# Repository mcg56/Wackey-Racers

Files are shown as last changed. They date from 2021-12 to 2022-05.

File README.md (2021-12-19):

Wacky Racers
===============

This contains a directory structure for your assignment.

doc -- documentation

hw  -- hardware (add your schematic PDF here)

src -- source code

Assignment instructions
-----------------------

The [instructions](https://eng-git.canterbury.ac.nz/wacky-racers/wacky-racers/-/raw/master/doc/instructions/instructions.pdf) are in a PDF file stored in this repository (you'll also get a copy when you fork the project).

Assignment guide
----------------

The [guide](https://eng-git.canterbury.ac.nz/wacky-racers/wacky-racers/-/raw/master/doc/guide/guide.pdf) is a PDF file stored in this repository (you'll also get a copy when you fork the project).

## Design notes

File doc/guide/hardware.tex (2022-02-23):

\chapter{System design}
\label{hardware}

The system requirements are specified in the assignment instructions.

\section{Recommendations}\label{recommendations}

\begin{enumerate}
\item
  Independently fuse the buck converter and H-bridge. This allows a fuse
  to be removed to isolate part of the circuit when finding a fault,
  such as a short across the power rails.

\item
  Have a zener diode to protect against overvoltage when your group
  member inadvertently cranks up the voltage from the bench power
  supply.

\item
  Have current limiting resistors for all off-board signals.

\item
  Have plenty of testpoints, especially for power supplies and
  signals.  You will never have enough!

\item
  Have at least one grunty ground testpoint for attaching a scope ground
  clip.

\item
  Have a dedicated PIO pin to drive a testpoint that you can use to
  trigger an oscilloscope for debugging.

\item
  Have the SAM4S erase pin connected to a test point close to a 3.3\,V
  testpoint. This is useful to completely erase the SAM4S flash memory
  when nothing works.

\item
  Have a MOSFET or servo interface for controlling something dastardly!

\end{enumerate}

\section{Standard chassis}

You can build your own racer or use the standard chassis.  The
standard chassis comes with:
%
\begin{itemize}
\item A pair of 6\,V DC motors.

\item A bumper with microswitch.

\item An on/off switch and fuse for the battery.

\item Battery and holder.
\end{itemize}
%
It is available from Diego in the Electronics Lab.  If you wish to
make your own chassis, Diego can supply the bumper, battery, and
motors.

\begin{figure}[!h]
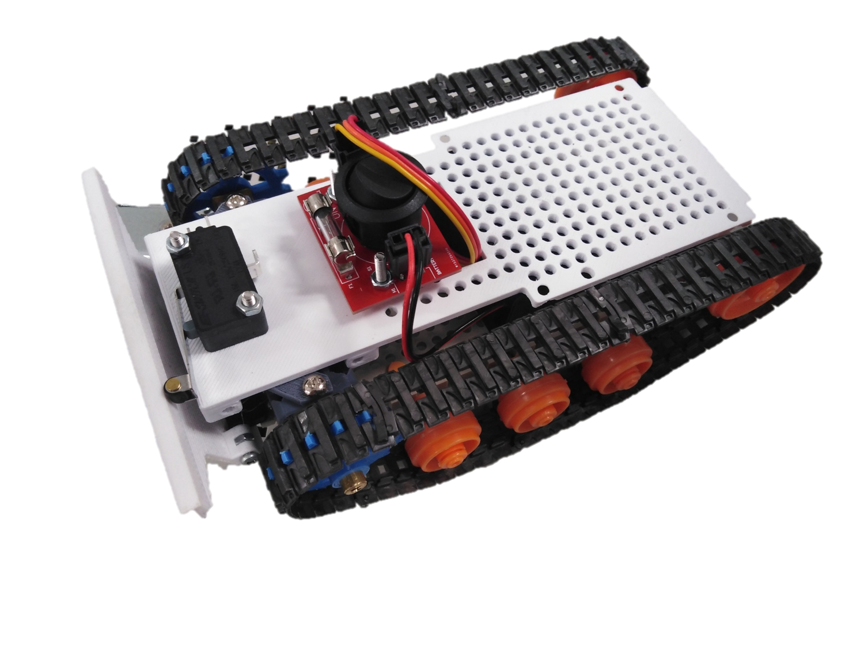
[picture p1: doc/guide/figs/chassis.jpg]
  \centering 
  \caption{Photo of the standard chassis.}
  \label{fig:chassis}
\end{figure}

\section{SAM4S MCU}\label{sam4s-mcu}

The SAM4S MCU is overkill for this assignment but is typical of ARM
processors used for bare-metal applications.  The particular chip we
are using is the SAM4S8B.  This was made by Atmel and is now owned by
Microchip.  The datasheet is available
at \url{https://www.microchip.com/en-us/product/ATSAM4S8B}.

The SAM4S8B has a 32-bit ARM Cortex M4 RISC CPU that can run at
120\,MHz and has 512\,KB of flash memory and 128\,KB of SRAM.

\subsection{Power pins}\label{power-pins}

The SAM4S has four grounds. They \textbf{must} all be connected. There
are also seven power pins. These \textbf{must} all be connected since
they power different parts of the chip. Note, some pins require 3.3\,V
while others require 1.2\,V. The 1.2\,V is generated by an internal
voltage regulator.

\subsection{Peripheral pins}\label{peripheral-pins}

\textbf{Many of the peripheral pins are dedicated and cannot be
  reassigned in software}, e.g., SPI, TWI, and USB pins. Note, there
are restrictions on the PWM pins.  See Table~11-2 in the SAM4S
datasheet for the pin assignments.  Also see \hyperref[PIO pins] {PIO
  pins} for electrical characteristics.

By default the \pin{PB4} and \pin{PB5} pins are configured for the
JTAG debugger.  These can be used for general PIO after setting an
internal bit.  See \protect\hyperref[disabling-jtag-pins]{disabling
JTAG pins}.

The logic levels are set by the voltage on the VDDIO pin (usually
3.3\,V).  \pin{PA12}--\pin{PA14} and \pin{PA26}--\pin{PA31} can
sink/source 4\,mA.  The USB pins (\pin{PB10}--\pin{PB11}) can
sink/source 30\,mA.  The rest can only sink/source 2\,mA of current.

The pullup and pulldown resistors are typically 100\,k$\Omega$.  On
reset, pullup resistors are enabled.

\subsection{USART/UART}\label{usartuart}

The SAM4S has two USARTs and two UARTs. The USARTs can emulate a
UART, have hardware flow control, and have a better driver so they are
recommended if you need a UART interface.

\subsection{PWM}\label{pwm}

The SAM4S can generate four independent PWM signals. There are
restrictions on which SAM4S pins they come out on. Note, the PWMLx and
PWMHx signals are complementary (i.e., one is low while the other is
high).

\subsection{TWI}\label{twi}

The SAM4S has two TWI peripherals (that can act as a master and
a slave) with dedicated TWD and TWCK pins. External pull-up resistors
are required.  TWI1 shares pins with JTAG; you will need to disable
JTAG in software.

\subsection{SPI}\label{spi}

The SAM4S has a single SPI peripheral with dedicated SCK, MISO, and
MOSI pins. Any PIO pin can be used for the chip select\footnote{For
  high speed operation (not needed for this assignment), you should
  use one of the dedicated chip select pins.}.

\subsection{ADC}\label{adc}

The SAM4S has a single ADC with a multiplexer to select one of a
number of analogue inputs.  It can sample at 1\,MHz.

\subsection{USB}\label{usb}

The SAM4S has a single USB peripheral connected to the DDP and DDM
pins. 27 ohm series termination resistors are required, placed close to
the SAM4S.

\section{Other chips}\label{other-chips}

\subsection{DRV8833 dual H-bridge}\label{drv8833-dual-h-bridge}

The DRV8833's datasheet is available at
\url{https://www.ti.com/product/DRV8833}.

The H-bridge has four modes: forward, reverse, slow decay (brake), and
fast decay (coast).  With slow decay mode, the motor is shorted so
that it stops faster.  With fast decay mode, the motor is
open-circuited and so it takes longer to stop.  However, there is
little difference in practice, due to friction in the gearbox.

If you want control over fast decay and slow decay in both forward and
reverse you will need \textbf{four} independent PWM signals. The SAM4S
can provide four independent PWM signals but be \textbf{careful} since
PWMxH and PWMxL are complementary signals driven from the same PWM
source.

If you are clever, you can drive the H-bridge with only two PWM
channels.  If you are not so clever, you will have fast decay in one
direction and slow decay in the other.

The capacitor connected to the bootstrap pin must be rated for
16\,V. The datasheet recommends an X7R dielectric.

\subsection{NRF24L01+ radio}

\begin{figure}[!h]
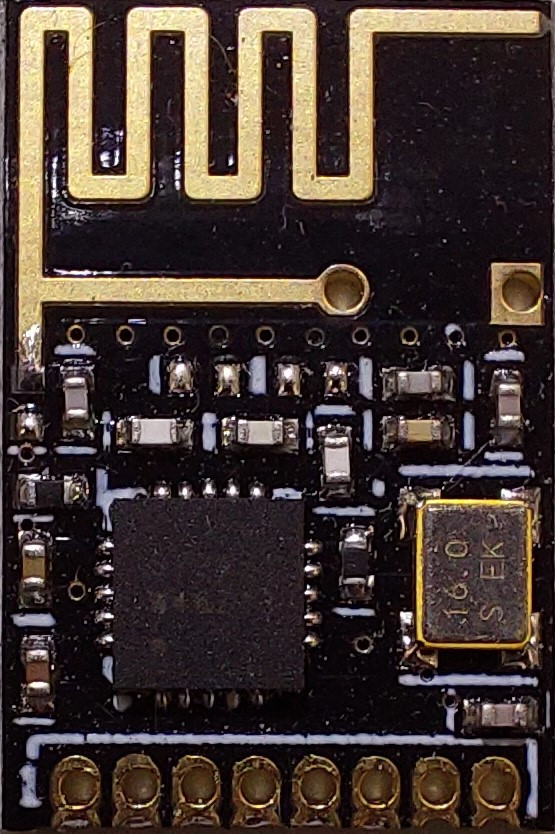
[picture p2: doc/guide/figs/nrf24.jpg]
  \centering 
  \caption{Photo of NRF24 radio.}
  \label{fig:nrf24}
\end{figure}

The nRF24 module we provide is actually a tiny PCB with all of the high
frequency analogue components populated for you. This module breaks out
the SPI communication pins, the power supply pins, and two signal pins
that you will need to connect to your microcontroller. The CE and IRQ
pins can both go to general PIO pins while the SPI pins (MOSI, MISO,
SCLK, CSN) need to be connected to the SAM4S SPI peripheral. The
nRF24L01 datasheet and other documentation for the breakout board is
available at \url{https://www.sparkfun.com/products/691}.

As this radio is ultimately an analogue circuit and any noise on the
power supply can affect the signal quality, we recommend using a
separate 3V3 regulator and using a low pass filter to provide the best
power.  Instead of a resistor, a ferrite bead is better.

\begin{figure}[h]
  \centering
  \begin{circuitikz}
    \draw (-1, 0) node[left] {\SI{3.3}{\volt}} to[R=\SI{1}{\ohm}, o-] (2, 0)
    to[C=\SI{10}{\micro\farad}, *-*] (2, -2);

    \draw (-1, -2) node[left] {GND} to[short, o-] (2, -2);
    \draw (2, 0) to[short] (4, 0);
    \draw (2, -2) to[short] (4, -2);
    \draw (6, 0.5) -- (4, 0.5) -- (4, -2.5) -- (6, -2.5);
    \node[right=0.2] at (4, 0) {VDD};
    \node[right=0.2] at (4, -2) {GND};
    \node at (6, -1) {nRF24};
  \end{circuitikz}
  \caption{Power supply filtering; a ferrite bead is better than a resistor.}
  \label{fig:radio-filtering}
\end{figure}

You cannot have a PCB plane near the antenna of the radio otherwise
the \textbf{range will be severely limited}.

The radio operates around 2.4 GHz and has 128 programmable channels,
each of 1 MHz.  Note, some of these channels use the same spectrum as
Bluetooth and WiFi.  A 5 byte address is appended to the start of each
transmission and the receiver will only respond when the address
matches.

The radio interfaces to the SAM4S using the SPI bus. The IRQ
pin is driven low to indicate a packet has been received.

\subsection{MPU9250 IMU}\label{mpu9250-imu}

This contains a three axis accelerometer, a three axis gyroscope, and a
three axis magnetometer. It appears that the magnetometer has been
bolted on to the accelerometers/gyroscopes and requires more hoop
jumping in software to make it work. Documentation is available at
\url{https://invensense.tdk.com/products/motion-tracking/9-axis/mpu-9250/}.

It has two different I2C addresses (0x68 and Ox69) depending on the
state of the AD0 pin.

\subsection{Buck converter}\label{buck-converter}

The buck converter is a switch-mode regulator that converts the
battery voltages to 5\,V DC.

\subsection{Voltage regulators}\label{voltage-regulators}

There are many flavours of \wikiref{voltage_regulators}{voltage regulator}.
Some are better for digital applications, some are better for analogue
applications, some are better for low power applications, etc.

If you are using a voltage regulator with an enable pin, do not forget
to allow for the time for the output voltage to ramp up. This can be
tens of milliseconds depending on the capacitive load and current draw.

Note, some regulators have pins that you must not connect. Some have
multiple pins for the same purpose; these must all be connected.

\section{External components}

\subsection{Battery}

The Wacky Racer batteries are Turnigy 5-cell 6\,V, 2300\,mAh, NiMH
with a three pin JST connector.  To preserve the battery life it is
imperative to not draw current when the battery voltage is below 5\,V.
Note, when fully charged, the battery voltage may be 7.5\,V.

The battery uses a standard RC servo connector: 3 pin 0.1'' (pin 1
GND, pin 2 5V, pin 3 NC). We suggest connecting both the first and
third pins to ground to allow the battery to be plugged in in both
orientations. The 461 Altium library has a component named
`Battery\_HEADER\_3pin' that is suitable to use.

\subsection{LED Tape}

The LED tape is a daisy-chained string of WS2812 smart LEDs.  These
LEDs use a clever mechanism to pass the RGB data down the
string\footnote{Each element consists of red, green, and blue LEDs
  with an 8-bit shift register to control the brightness for each
  colour.  These shift registers are chained together.} with different
pulse lengths for 1 and 0.  They are connected as shown in
\reffig{LED-chaining}.

\begin{figure}[h]
  \centering
  \begin{circuitikz}

    \draw (0, 0) node[left] {\SI{5}{\volt}} to[short, o-] (13, 0);
    \draw (0, -4) node[left] {GND} to[short, o-] (13, -4);

    \draw (1, -1) rectangle (4, -3);
    \draw (5, -1) rectangle (8, -3);
    \draw (9, -1) rectangle (12, -3);

    \draw (0, -2) node[left] {DIN} to[short, o-] (1, -2) node[right] {DIN};
    \draw (4, -2) node[left] {DO} -- (5, -2) node[right] {DIN};
    \draw (8, -2) node[left] {DO} -- (9, -2) node[right] {DIN};
    \draw (12, -2) node[left] {DO} -- (13, -2);

    \draw (2.5, 0) -- (2.5, -1) node[below] {VDD};
    \draw (6.5, 0) -- (6.5, -1) node[below] {VDD};
    \draw (10.5, 0) -- (10.5, -1) node[below] {VDD};

    \draw (2.5, -4) -- (2.5, -3) node[above] {GND};
    \draw (6.5, -4) -- (6.5, -3) node[above] {GND};
    \draw (10.5, -4) -- (10.5, -3) node[above] {GND};
  \end{circuitikz}
  \caption{Chaining of smart LEDs in the LED-tape.}
  \label{fig:LED-chaining}
\end{figure}

This means you will need to provide a three pin header (0.1" standard
header) with the pinout: pin 1 \SI{5}{\volt}, pin 2 signal, pin 3
ground. Each individual LED has a maximum supply current
of \SI{60}{\milli\ampere} (\SI{20}{\milli\ampere} per red, green, blue
channel). We will provide up to half a metre of LED tape to each car
or hat, giving a maximum number of 30 LEDs to be driven.

\begin{figure}[!h]
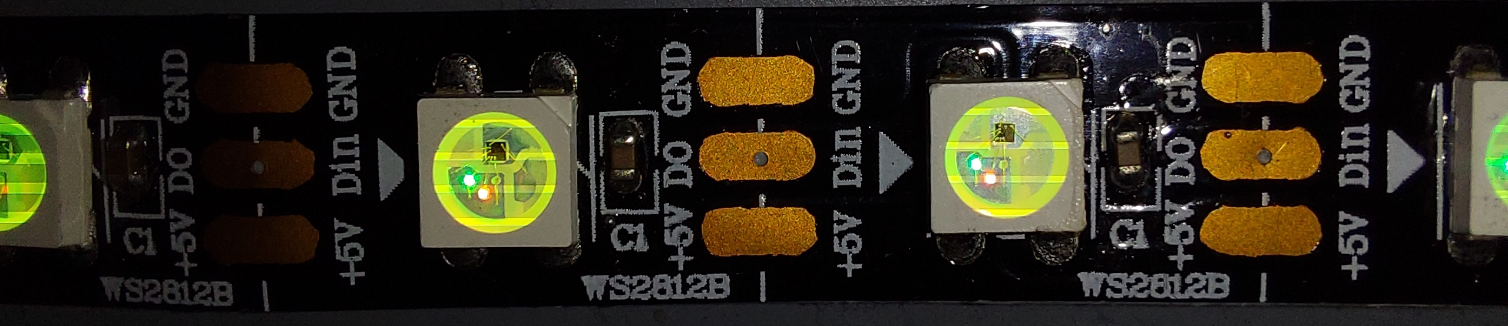
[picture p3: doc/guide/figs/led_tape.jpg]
  \centering 
  \caption{Photo of a section of LED tape.}
  \label{fig:led-tape}
\end{figure}

\subsection{Bumper}

The provided bumper senses the contact through a simple limit switch. This
switch is normally open and on contact will close.

\begin{figure}[h]
  \centering
  \begin{circuitikz}

    \draw (0, 0) to[short, o-*] (2, 0) to[switch] (2, -2) node[ground]{};
    \draw (2, 0) to[R] (2, 2) node[vcc]{\SI{3.3}{\volt}};

    \draw[blue, dashed] (1.5, -0.5) rectangle (2.5, -1.5);
    \node[blue, right] at (2.5, -1) {limit switch};

  \end{circuitikz}
\end{figure}

Note that the pullup resistor shown could simply be the internal
pullup resistor on a PIO pin. The connector for the limit switch
should be a simple 2 pin 0.1" header.

\subsection{Buzzer}

The buzzers supplied are passive piezo-electric devices. Applying a
voltage across the two terminals causes the element to
deform. Applying an alternating current to the device generates an
audible tone. The larger the applied voltage differential, the louder
the tone becomes. There are plenty of example circuits for piezo
buzzers available online.  Note, you need to be able to charge and
discharge the capacitance of the pizeocrystal.

\subsection{Motors}

The motors available in the provided chassis are \SI{6}{\volt} DC
motors. These have a low DC resistance and will take as much current
as the DRV8833 motor driver can supply. You need to add connectors for
the motors, either 2 pin 0.1" headers or screw terminals are
suggested.

\subsection{Connectors}

\begin{enumerate}
\item USB micro or mini connector for debugging
\item 3 pin 0.1'' for LED tape (pin 1 5\,V, pin 2 signal, pin 3 ground)
\item 2 pin 0.1'' for bumper (pin 1 switch, pin 2 ground)
\item 10 pin IDE for serial wire debug
\item 3 pin JR battery connector (pin 1 GND, pin 2 VBAT, pin 3 GND)
\item motor connectors (for Racer)
\item connectors for dastardly stuff
\end{enumerate}

\section{Other components}

\begin{enumerate}
\item We recommend that you use components in the ECE Altium library.
  These are stocked in the SMT lab.  For any other components you may
  require, see Scott Lloyd in the SMT lab.
\end{enumerate}

\section{Reading datasheets}

The manufacturer will tell you what they are proud of on the first
page.  They will omit details of poor aspects.

There is a knack in reading a large datasheet.  Here's what I do
first:

\begin{enumerate}
\item Look at the example circuits.

\item Read the absolute maximum ratings.

\item Read the pin definitions.
\end{enumerate}

% SAM4S hardware checklist

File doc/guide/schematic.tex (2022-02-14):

\chapter{Schematic}

\section{Altium tutorial}

See the ENCE461 Learn page for the Altium tutorial.

\section{Suggestions}

\begin{enumerate}
\item If you get the schematic wrong, the PCB will be wrong, and you
  will have rework grief (see \hyperref[rework]{rework}).

\item A clear schematic is important for debugging.

\item In general, you should aim to have inputs on the left, outputs
  on the right, higher voltages at the top.

\item Add notes to explain anything non-obvious.
\end{enumerate}

\section{Check list}
\label{schematic-check-list}

You must check the schematic carefully.  I use a highlighter to mark
every wire and component.  If you get the schematic wrong, the PCB
will be wrong, and you will have to do much rework, see
\reffig{rework}.

\begin{figure}[!h]
  \centering
  
  \caption{Example of a PCB where not much care was taken with the
    schematic resulting in a lot of rework.  And yes, the board worked
    in the end.}
  \label{fig:rework}
\end{figure}

\begin{enumerate}
\item
  The SPI signals for the radio are connected to the correct MCU pins.
\item
  The PWM signals for the motor are connected to the correct MCU pins.
  Note, the PWMLx and PWMHx pins are complementary and cannot be driven
  independently.
\item
  All the MCU VDD pins need to be powered.
\item
  All the MCU GND pins need to be powered.
\item
  Avoid connecting to \pin{PB4} and \pin{PB5} (say for TWI1).  If you
  do you will need to disable JTAG in software.
\end{enumerate}

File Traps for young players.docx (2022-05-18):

# Programming

- OpenOCD not recognised? Launch VScode through vscode.bat in wacky racers.
- Did you run openOCD?
- Maybe try run bootloader.
- Not uploading? Unplug power supply

# Board operation

- Board not working like it should? Check pins in the configuration file target.h are correct.
- Make sure you use the correct target (hat vs racer)
- Make sure the correct silk screen label is used. Eg Level shifters silk screens underneath on hat.
- Never copy code! Be especially careful if copying C++ code to C as functions with the same name can do different things.
- Make sure you bracket multi line if statements.
- Try revert back to original micheal code (worst case scenario)

## Power

- ST-Link does not provide power to anything other than the chip
- USB does not provide LED Tape power

## Strange things that are normal

- Unconfigured LED’s will glow dim

# Nothings working

- Did you put it on metal and short pins?
- Power supply is on?
- If you unplugged the board from power, try pressing nrst. Especially if you are using USB

# Future thing to do

- Don’t send ascii characters for radio, send raw bytes which need to be decoded instead, much less data to send.

# Debugger

GDB offers a big list of commands, however the following commands are the ones used most frequently:

- b main - Puts a breakpoint at the beginning of the program
- b - Puts a breakpoint at the current line
- b N - Puts a breakpoint at line N
- b +N - Puts a breakpoint N lines down from the current line
- b fn - Puts a breakpoint at the beginning of function "fn"
- d N - Deletes breakpoint number N
- info break - list breakpoints
- r - Runs the program until a breakpoint or error
- c - Continues running the program until the next breakpoint or error
- f - Runs until the current function is finished
- s - Runs the next line of the program
- s N - Runs the next N lines of the program
- n - Like s, but it does not step into functions
- u N - Runs until you get N lines in front of the current line
- p var - Prints the current value of the variable "var"
- bt - Prints a stack trace
- u - Goes up a level in the stack
- d - Goes down a level in the stack
- q - Quits gdb

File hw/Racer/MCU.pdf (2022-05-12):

# USB SAM4S

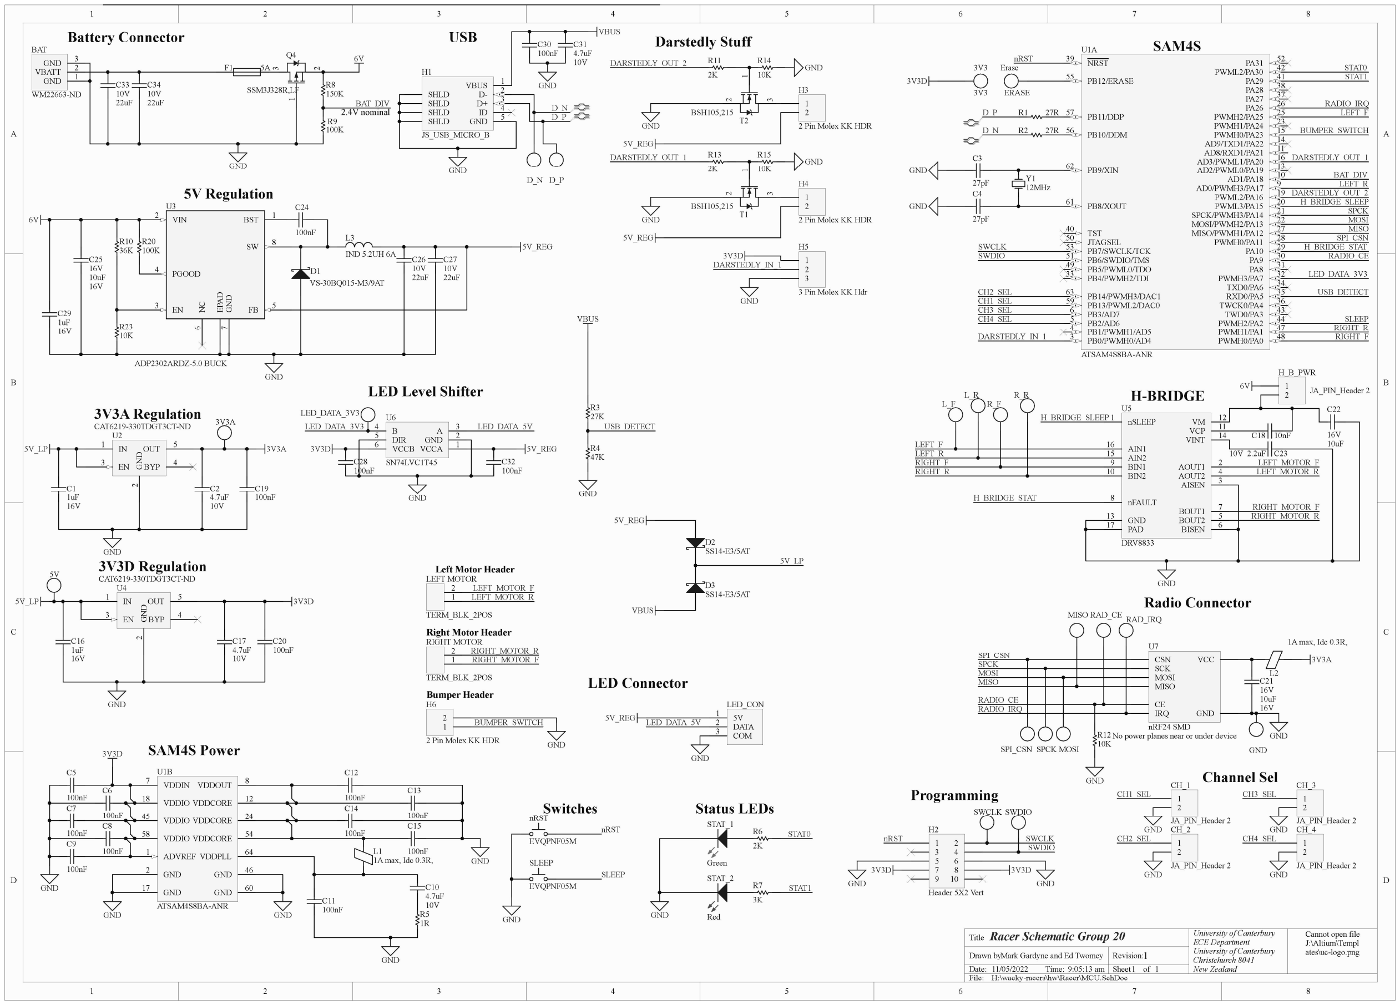
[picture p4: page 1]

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
University of Canterbury
ECE Department
University of Canterbury
Christchurch 8041

### 1 New Zealand

## Racer Schematic Group 20

1
11/05/2022 | 9:05:13 am
H:\wacky-racers\hw\Racer\MCU.SchDoc

Title

Drawn by:
Date:
File:

Revision:
Time: | Sheet | of

Mark Gardyne and Ed Twomey

Cannot open file
J:\Altium\Templ
ates\uc-logo.png
IN 1 | GND

2

EN 3 | BYP | 4
| OUT | 5

CAT6219-330TDGT3CT-ND
U2

JTAGSEL 50

NRST 39

PWMH0/PA0 | 48 PWMH1/PA1 | 47 PWMH2/PA2 | 44 TWD0/PA3 | 43 TWCK0/PA4 | 36 RXD0/PA5 | 35 TXD0/PA6 | 34 PWMH3/PA7 | 32 PA8 | 31 PA9 | 30 PA10 | 29 PWMH0/PA11 | 28 MISO/PWMH1/PA12 | 27 MOSI/PWMH2/PA13 | 22 SPCK/PWMH3/PA14 | 21 PWML3/PA15 | 20 PWML2/PA16 | 19 AD0/PWMH3/PA17 | 9
AD1/PA18 | 10 AD2/PWML0/PA19 | 13 AD3/PWML1/PA20 | 16 AD8/RXD1/PA21 | 11 AD9/TXD1/PA22 | 14 PWMH0/PA23 | 15 PWMH1/PA24 | 23 PWMH2/PA25 | 25 PA26 | 26 PA27 | 37 PA28 | 38 PA29 | 41 PWML2/PA30 | 42 PA31 | 52

PB0/PWMH0/AD4 3

PB1/PWMH1/AD5 4

PB2/AD6 5

PB3/AD7 6

PB4/PWMH2/TDI 33 | PB5/PWML0/TDO 49 | PB6/SWDIO/TMS 51 | PB7/SWCLK/TCK 53

PB8/XOUT 61

PB9/XIN 62

PB10/DDM 56

PB11/DDP 57

PB12/ERASE 55

PB13/PWML2/DAC0 59 PB14/PWMH3/DAC1 63

TST 40

U1A

ATSAM4S8BA-ANR

GND 2

GND 17

GND | 46
GND | 60
VDDCORE | 12
VDDCORE | 24
VDDCORE | 54

VDDIO 18

VDDIO 45

VDDIO 58

VDDPLL | 64 ADVREF 1
VDDOUT | 8 VDDIN 7

U1B

ATSAM4S8BA-ANR

VBUS | 1
D- | 2
D+ | 3
ID | 4
GND | 5 SHLD

SHLD

SHLD

SHLD

H1

JS_USB_MICRO_B

nRST

EVQPNF05M

SLEEP

EVQPNF05M

Red

STAT_2

Green

STAT_1

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
Header 5X2 Vert

# 3V3A Regulation

# Programming

Switches | Status LEDs

# SAM4S Power

5V_LP

1uF
16V

C1
4.7uF
10V

C2

3V3A

GND

GND

VBUS

D_N
D_P | D_P
| D_N

VBUS

GND

USB_DETECT

27K

R3

47K

R4

USB_DETECT

GND | GND
3V3D | 3V3D SWCLK SWDIO

nRST

SWDIO

SWCLK

12MHz

Y1 27pF

C3

27pF

C4

GND

GND

3V3

3V3

ERASE

Erase
3V3D

3V3D

GND

GND | GND

100nF

C5

100nF

C6

100nF

C7

100nF

C8

100nF

C9

100nF

C11

GND

1R

R5

4.7uF
10V

C10

GND

100nF

C12

100nF

C13

100nF

C14

100nF

C15

1A max, Idc 0.3R,

L1

STAT0

STAT1

RIGHT_F

RIGHT_R

SLEEP

GND

nRST

SLEEP

FB | 5
VIN 2 | BST | 1 NC | EPAD

6

PGOOD 4

EN 3

SW 8 GND

7

U3

ADP2302ARDZ-5.0 BUCK

# 5V Regulation

IN 1 | GND

2

EN 3 | BYP | 4
| OUT | 5

CAT6219-330TDGT3CT-ND
U4

# 3V3D Regulation

5V_LP

1uF
16V

C16
4.7uF
10V

C17

3V3D

GND

GND | 1
VBATT | 2
GND | 3

WM22663-ND

BAT

# Battery Connector

5V 1
DATA 2
COM 3

LED_CON

# LED Connector

GND

5V_REG

LED_DATA_3V3

LED_DATA_5V

BUMPER_SWITCH

RADIO_CE

H_BRIDGE_STAT

MISO

MOSI

SPCK

nSLEEP 1

AOUT1 | 2
AISEN | 3
AOUT2 | 4
BOUT2 | 5
BISEN | 6
BOUT1 | 7

nFAULT 8

BIN1 9
BIN2 10
VCP | 11 VM | 12

GND 13

VINT | 14
AIN2 15 | AIN1 16

PAD 17

U5

DRV8833

LEFT_R

LEFT_F

LEFT_F
LEFT_R
RIGHT_F
RIGHT_R

C18 10nF

1

2

LEFT MOTOR

TERM_BLK_2POS

1

2

RIGHT MOTOR

TERM_BLK_2POS

# H-BRIDGE

### Left Motor Header

### Right Motor Header

LEFT_MOTOR_F
LEFT_MOTOR_R

RIGHT_MOTOR_F

RIGHT_MOTOR_R

LEFT_MOTOR_F
LEFT_MOTOR_R

RIGHT_MOTOR_F
RIGHT_MOTOR_R
100nF | H_BRIDGE_STAT

C19

3V3A

5V

100nF

C20

VCCA | 1
GND | 2

A

### 3 B

4
DIR 5
VCCB 6

U6

SN74LVC1T45

# LED Level Shifter

3V3D | 5V_REG
LED_DATA_3V3 | LED_DATA_5V

GND

SPI_CSN

RADIO_IRQ

### Bumper Header

BUMPER_SWITCH

GND

GND

L_F

MOSI

D_N D_P

GND

# Radio Connector

1
2

CH_1

JA_PIN_Header 2

1
2

CH_3

JA_PIN_Header 2

1
2

CH_2

JA_PIN_Header 2

1
2

CH_4

JA_PIN_Header 2

CH1_SEL

CH2_SEL

CH3_SEL
CH4_SEL

CH1_SEL

CH2_SEL

CH3_SEL

CH4_SEL

# Channel Sel

nRST

6V

10V | C23 2.2uF

GND

DARSTEDLY_OUT_1

# Darstedly Stuff

3V3D

GND

DARSTEDLY_IN_1

DARSTEDLY_IN_1

GND

10K

R23

100K

R20

100nF

C24

10V
22uF

C26
10V
22uF

C27

1uF
16V

C29

H_BRIDGE_SLEEP

H_BRIDGE_SLEEP

4.7uF
10V

C31
100nF

C30

GND

6V

BAT_DIV

GND
BAT_DIV

DARSTEDLY_OUT_2

GND

DARSTEDLY_OUT_2

F1 5A

16V
10uF
16V

C25

16V
10uF

C22

2.4V nominal

5V_REG

VCC

GND

CE

CSN
SCK
MOSI
MISO

IRQ

No power planes near or under device

U7

nRF24 SMD
GND

6V

16V
10uF
16V

C21

1A max, Idc 0.3R,

L2

3V3A

RADIO_IRQ

MISO

MOSI

SPI_CSN
SPCK

RADIO_CE

100K

R9

MISO RAD_CE RAD_IRQ

SPI_CSN SPCK

150K

R8

GND

GND | GND GND

LED_DATA_3V3

L3
IND 5.2UH 6A

D1
VS-30BQ015-M3/9AT

L_R
R_F

R_R

SWCLK SWDIO

2K

R6

3K

R7

10K

R12

GND

100nF

C32
100nF

C28

SSM3J328R,LF ³

1

2

Q4

1
2

H_B_PWR

JA_PIN_Header 2

5V_LP

VBUS

5V_REG

5V_REG

SS14-E3/5AT

D3

SS14-E3/5AT

D2

STAT1

STAT0

BSH105,215 | 3

1

2

T2

2K

R11

DARSTEDLY_OUT_1

GND

5V_REG

BSH105,215 | 3

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
### 2 Pin Molex KK HDR

1
2

H3

### 2 Pin Molex KK HDR

1
2

H4

1
2

### 3 Pin Molex KK Hdr

3

H5

### 2 Pin Molex KK HDR

1

2

H6

R1 | 27R
R2 | 27R

10V
22uF

C33
10V
22uF

C34

36K

R10

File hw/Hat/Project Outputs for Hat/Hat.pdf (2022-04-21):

Comment | Description | Designator | Footprint | LibRef | Quantity
10uF | CAP CER 10uF X5R 16V 0805 C1, C21, C42 | | CAPC2012L | CC_10uF_0805_16V | 3
27pF | CAP CER 27pF NPO/COG +-5% 50V 0603 C2, C25 | | CAPC1608L | CC_27pF_0603 | 2
1uF | CAP CER 1uF Y5V -20% +80% 16V 0603 C3, C16, C29, C30 | | CAPC1608L | CC_1uF_0603 | 4
4.7uF | CAP CER 4.7uF X5R +-20% 10V 0603 C4, C15, C17 | | CAPC1608N | CC_4.7uF_0603 | 3
100nF | CAP CER 100nF X7R +-10% 50V 0603 C5, C6, C7, C8, C9, C10, C11, C12, C13, C14, C18, C20, C22, C23, C24, C28, C31, C32, C33, C34, C35, C36, C37, C38, C39, C40, C41 CAPC1608L | | | CC_100nF_0603 | 27
10nF | CAP CER 10nF X7R +-10% 50V 0603 C19 | | CAPC1608L | CC_10nF_0603 | 1
22uF | CAP CER 22uF Y5V -20% +80% 10V 1206 C26, C27 | | CAPC3216L | CC_22uF_1206 | 2
VS-30BQ015-M3/9AT | DIODE, SCHOTTKY, 3A, 15V, DO-214AB / SMC D1 | | SMC | DS_VS-30BQ015-M3 | 1
SS14-E3/5AT | DIODE, SCHOTTKY, 1A, 40V, DO-214AC D2, D3 | | DIOM4227X23N | DS_SS14E3 | 2
Red | LED Red 250mcd 0603 SMD DL1 | | WL-SMCW0603 | DL_150060RS75000 | 1
Green | LED Green 430mcd 0603 SMD DL2 | | WL-SMCW0603 | DL_150060GS75000 | 1
2A | Fuse 2.0A Very Fast Acting 1206 SMD F1 | | RESC3216N | FS_Fuse_2.0A | 1
0.25A | Fuse 0.25A Very Fast Acting 1206 SMD F2 | | RESC3216N | FS_Fuse_0.25A | 1
JS_USB_MICRO_B | CONN USB MICRO B RECPT SMT R/A H1 | | FCI_USB_10118194-0001LF JS_USB_MICRO_B_SMT | | 1
Header 5X2 Vert | IDC Header, 2,54mm, 10-Pin, Vert H2 | | IDC2.54-V10D | JA_HDR_IDC_5X2_VERT | 1
Battery_HEADER_3pin | 3Pin Header 2.54mm spacing Digikey #WM22663-ND | H3 | BATT_HEADER_3POS Battery_HEADER_3pin | | 1
LED_Strip | CONN HEADER 3POS 2.54mm VERT_Thru Hole H4 | | MOLEX_KK_3_HDR | LED_Strip_Header | 1
1A max, Idc 0.3R, | Ferrite Bead, Rdc 0.3R, Z100MHZ 600R, Imax 1A, SMD 1206 L1, L3 | | INDC3216L | IN_Ferrite-Bead | 2
IND 5.2UH 6A | FIXED IND 5.2UH 6A 22 MOHM SMD L2 | | INDUCTOR5u2 | CDRH104RNP-5R2NC | 1
CH1 | Header, 2-Pin | P2 | HDR1X2 | JA_PIN_Header 2 | 1
CH2 | Header, 2-Pin | P3 | HDR1X2 | JA_PIN_Header 2 | 1
CH3 | Header, 2-Pin | P4 | HDR1X2 | JA_PIN_Header 2 | 1
GPIO_Header | Header, 6-Pin | P5 | HDR1X6 | JA_PIN_Header 6 | 1
CH4 | Header, 2-Pin | P6 | HDR1X2 | JA_PIN_Header 2 | 1
Joy_sel | Header, 2-Pin | P7 | HDR1X2 | JA_PIN_Header 2 | 1
Servo | Header, 3-Pin | P8 | HDR1X3 | JA_PIN_Header 3 | 1
Piezo Buzzer | TDK - PS1240P02BT - BUZZER, PIEZO, 70DB, 12.2MM P9 | | BUZZER | Piezo Buzzer | 1
LS1 | Header, 3-Pin | P11 | HDR1X3 | JA_PIN_Header 3 | 1
LS2 | Header, 3-Pin | P12 | HDR1X3 | JA_PIN_Header 3 | 1
Spare | Header, 2-Pin | P13 | HDR1X2 | JA_PIN_Header 2 | 1
BC817W | NPN GP Bipolar Transistor 45V 500mA SOT323 Q1 | | SOT323_M | TB_BC817W | 1
SSM3J328R,LF | MOSFET P-CH 20V 6A SOT23-3 Q2 | | SOT23_L | TM_SSM3J328R | 1
27K | RES 27K OHM 1/10W 5% 0603 SMD R1 | | RESC1608L | RS_27K | 1
47K | RES 47.0K OHM 1/10W 5% 0603 SMD R2 | | RESC1608N | RS_47K | 1
150K | RES 150K OHM 1/10W 5% 0603 SMD R3 | | RESC1608L | RS_150K | 1
100K | RES 100K OHM 1/10W 5% 0603 SMD R4, R31 | | RESC1608L | RS_100K | 2
3K | RES 3K OHM 1/10W 5% 0603 SMD R5 | | RESC1608L | RS_3K | 1
2K | RES 2K OHM 1/10W 5% 0603 SMD R6 | | RESC1608L | RS_2K | 1
27R | RES 27 OHM 1/10W 5% 0603 SMD R8, R24 | | RESC1608L | RS_27R | 2
2K2 | RES 2.2K OHM 1/10W 5% 0603 SMD R18, R19 | | RESC1608L | RS_2K2 | 2
1K | RES 1.0K OHM 1/10W 5% 0603 SMD R21, R22 | | RESC1608L | RS_1K | 2
1R | RES 1R OHM 1/4W 5% 1206 SMD R23 | | RESC3216L | RT_1R | 1
10K | RES 10.0K OHM 1/10W 5% 0603 SMD R27, R34 | | RESC1608L | RS_10K | 2
24K | RES 24K OHM 1/10W 5% 0603 SMD R29 | | RESC1608L | RS_24K | 1
nRST | Panasonic 6 x 3.5mm SMD Light Touch Switch Type SMD S1 | | EVQPNF05M | WS_EVQPNF05M | 1
SLEEP | Panasonic 6 x 3.5mm SMD Light Touch Switch Type SMD S2 | | EVQPNF05M | WS_EVQPNF05M | 1
ATSAM4S8BA-ANR | IC MCU 32BIT 512KB FLASH 64LQFP U1 | | LQFP64_L | SE_ATSAM4S16BA-MU | 1
CAT6219-330TDGT3 | IC REG LIN 3.3V 500MA TSOT23-5 U2, U4 | | SOT95P280X145-5N | SV_CAT6219-330TDGT3 | 2
ADP2302ARDZ-5.0 BUCKIC REG BUCK 5V 2A 8SOIC U3 | | | RD_8_1 | ADP2302ARDZ-5.0-R7 | 1
MPU-9250 | 9 axis IMU | U5 | QUAD24 | MPU-9250 | 1
SN74LVC1T45 | 1.8V - 5V level converter U7, U8, U9 | | SOT23-6_N | SN74LVC1T45 | 3
nRF24 SMD | nRF24 SMD Module | U10 | NRF24 | NRF24 | 1
Joystick 10k with Sw | JOYSTICK 10K OHM 2 AXIS TH VR1 | | Joystick_Sw | Joystick 10k with Sw | 1
12MHz | CRYSTAL 12MHZ 18PF 6X3.5mm SMD Y1 | | 6.0X3.5-4 | XT_CRYSTAL_12MHz_18pF | 1

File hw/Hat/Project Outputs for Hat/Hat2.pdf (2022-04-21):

Altium Limited Confidential | 22/04/2022 | Page

1

Bill of Materials | Bill of Materials for PCB Document [hat.PcbDoc]
Source Data From: | hat.PcbDoc
Project: | | Hat.PrjPcb
Variant: | | None
Creation Date: 22/04/2022 | 8:01 AM
Print Date: | 22-Apr-22 | 8:01:15 AM
Footprint | Comment | LibRef | Designator | Description | Quantity
CAPC2012L | 10uF | CC_10uF_0805_16VC1, C21, C42 | CAP CER 10uF X5R 16V 0805

3
CAPC1608L | 27pF | CC_27pF_0603 | C2, C25 | CAP CER 27pF NPO/COG +-5% 50V 0603

2
CAPC1608L | 1uF | CC_1uF_0603 | C3, C16, C29, C30 | CAP CER 1uF Y5V -20% +80% 16V 0603

4
CAPC1608N | 4.7uF | CC_4.7uF_0603 | C4, C15, C17 | CAP CER 4.7uF X5R +-20% 10V 0603

3
CAPC1608L | 100nF | CC_100nF_0603 C5, C6, C7, C8, C9, C10, C11, C12, C13,
| | | C14, C18, C20, C22, C23, C24, C28, C31, C32, C33, C34, C35, C36, C37, C38, C39, C40, C41 | CAP CER 100nF X7R +-10% 50V 0603 | 27
CAPC1608L | 10nF | CC_10nF_0603 | C19 | CAP CER 10nF X7R +-10% 50V 0603

1
CAPC3216L | 22uF | CC_22uF_1206 | C26, C27 | CAP CER 22uF Y5V -20% +80% 10V 1206

2
SMC | VS-30BQ015-M3/9AT DS_VS-30BQ015-M3 D1 | DIODE, SCHOTTKY, 3A, 15V, DO-214AB / SMC

1
DIOM4227X23NSS14-E3/5AT | DS_SS14E3 | D2, D3 | DIODE, SCHOTTKY, 1A, 40V, DO-214AC

2
WL-SMCW0603Red | DL_150060RS75000 DL1 | LED Red 250mcd 0603 SMD

1
WL-SMCW0603Green | DL_150060GS75000 DL2 | LED Green 430mcd 0603 SMD

1
RESC3216N | 2A | FS_Fuse_2.0A | F1 | Fuse 2.0A Very Fast Acting 1206 SMD

1
RESC3216N | 0.25A | FS_Fuse_0.25A | F2 | Fuse 0.25A Very Fast Acting 1206 SMD

1
FCI_USB_10118194-0001LF JS_USB_MICRO_BJS_USB_MICRO_B_SMT H1 | CONN USB MICRO B RECPT SMT R/A

1
IDC2.54-V10DHeader 5X2 Vert | JA_HDR_IDC_5X2_VERT H2 | IDC Header, 2,54mm, 10-Pin, Vert

1
BATT_HEADER_3POS Battery_HEADER_3pin Battery_HEADER_3pin H | 3Pin Header 2.54mm spacing
| | | | Digikey #WM22663-ND

1

MOLEX_KK_3_HDR LED_Strip | LED_Strip_HeaderH4 | CONN HEADER 3POS 2.54mm VERT_Thru Hole

1
INDC3216L | 1A max, Idc 0.3R,IN_Ferrite-Bead | L1, L3 | Ferrite Bead, Rdc 0.3R, Z100MHZ 600R, Imax 1A, SMD 1206 2
INDUCTOR5u2IND 5.2UH 6A | CDRH104RNP-5R2NC L2 | FIXED IND 5.2UH 6A 22 MOHM SMD

1
HDR1X2 | CH1 | JA_PIN_Header 2P2 | Header, 2-Pin

1
HDR1X2 | CH2 | JA_PIN_Header 2P3 | Header, 2-Pin

1
HDR1X2 | CH3 | JA_PIN_Header 2P4 | Header, 2-Pin

1
HDR1X6 | GPIO_Header | JA_PIN_Header 6P5 | Header, 6-Pin

1
HDR1X2 | CH4 | JA_PIN_Header 2P6 | Header, 2-Pin

1
HDR1X2 | Joy_sel | JA_PIN_Header 2P7 | Header, 2-Pin

1
HDR1X3 | Servo | JA_PIN_Header 3P8 | Header, 3-Pin

1
BUZZER | Piezo Buzzer | Piezo Buzzer | P9 | TDK - PS1240P02BT - BUZZER, PIEZO, 70DB, 12.2MM1
HDR1X3 | LS1 | JA_PIN_Header 3P11 | Header, 3-Pin
| | | | 1
HDR1X3 | LS2 | JA_PIN_Header 3P12 | Header, 3-Pin
| | | | 1
HDR1X2 | Spare | JA_PIN_Header 2P13 | Header, 2-Pin
| | | | 1
SOT323_M | BC817W | TB_BC817W | Q1 | NPN GP Bipolar Transistor 45V 500mA SOT323
| | | | 1
SOT23_L | SSM3J328R,LF | TM_SSM3J328R Q2 | MOSFET P-CH 20V 6A SOT23-3
| | | | 1
RESC1608L | 27K | RS_27K | R1 | RES 27K OHM 1/10W 5% 0603 SMD
| | | | 1
RESC1608N | 47K | RS_47K | R2 | RES 47.0K OHM 1/10W 5% 0603 SMD
| | | | 1
RESC1608L | 150K | RS_150K | R3 | RES 150K OHM 1/10W 5% 0603 SMD
| | | | 1
RESC1608L | 100K | RS_100K | R4, R31 | RES 100K OHM 1/10W 5% 0603 SMD
| | | | 2
RESC1608L | 3K | RS_3K | R5 | RES 3K OHM 1/10W 5% 0603 SMD
| | | | 1
RESC1608L | 2K | RS_2K | R6 | RES 2K OHM 1/10W 5% 0603 SMD
| | | | 1
RESC1608L | 27R | RS_27R | R8, R24 | RES 27 OHM 1/10W 5% 0603 SMD
| | | | 2
RESC1608L | 2K2 | RS_2K2 | R18, R19 | RES 2.2K OHM 1/10W 5% 0603 SMD
| | | | 2
RESC1608L | 1K | RS_1K | R21, R22 | RES 1.0K OHM 1/10W 5% 0603 SMD
| | | | 2
RESC3216L | 1R | RT_1R | R23 | RES 1R OHM 1/4W 5% 1206 SMD
| | | | 1
RESC1608L | 10K | RS_10K | R27, R34 | RES 10.0K OHM 1/10W 5% 0603 SMD
| | | | 2
RESC1608L | 24K | RS_24K | R29 | RES 24K OHM 1/10W 5% 0603 SMD
| | | | 1
EVQPNF05M | nRST | WS_EVQPNF05MS1 | Panasonic 6 x 3.5mm SMD Light Touch Switch Type SMD 1
EVQPNF05M | SLEEP | WS_EVQPNF05MS2 | Panasonic 6 x 3.5mm SMD Light Touch Switch Type SMD 1
LQFP64_L | ATSAM4S8BA-ANRSE_ATSAM4S16BA-MU U1 | IC MCU 32BIT 512KB FLASH 64LQFP
| | | | 1
SOT95P280X145-5N CAT6219-330TDGT3 SV_CAT6219-330TDGT3 U2, U4 | IC REG LIN 3.3V 500MA TSOT23-5
| | | | 2
RD_8_1 | ADP2302ARDZ-5.0 BUCK ADP2302ARDZ-5.0-R7 U3 | IC REG BUCK 5V 2A 8SOIC
| | | | 1
QUAD24 | MPU-9250 | MPU-9250 | U5 | 9 axis IMU
| | | | 1
SOT23-6_N | SN74LVC1T45 | SN74LVC1T45 | U7, U8, U9 | 1.8V - 5V level converter
| | | | 3
NRF24 | nRF24 SMD | NRF24 | U10 | nRF24 SMD Module
| | | | 1
Joystick_Sw | Joystick 10k with SwJoystick 10k with SwVR1 | JOYSTICK 10K OHM 2 AXIS TH
| | | | 1
6.0X3.5-4 | 12MHz | XT_CRYSTAL_12MHz_18pF Y1 | CRYSTAL 12MHZ 18PF 6X3.5mm SMD
| | | | 1
| | | | 99
Approved | | Notes

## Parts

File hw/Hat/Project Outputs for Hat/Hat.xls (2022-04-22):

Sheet: BOM Report
Bill of Materials |  |  | Bill of Materials for PCB Document [hat.PcbDoc]
Source Data From: |  | hat.PcbDoc
Project: |  | Hat.PrjPcb
Variant: |  | None
Creation Date: | 22/04/2022 | 8:21 AM
Print Date: | 2022-04-22 | 8:21:46
Footprint | Comment | LibRef | Designator | Description | Quantity
CAPC2012L | 10uF | CC_10uF_0805_16V | C1, C21, C42 | CAP CER 10uF X5R 16V 0805 | 3
CAPC1608L | 27pF | CC_27pF_0603 | C2, C25 | CAP CER 27pF NPO/COG +-5% 50V 0603 | 2
CAPC1608L | 1uF | CC_1uF_0603 | C3, C16, C29, C30 | CAP CER 1uF Y5V -20% +80% 16V 0603 | 4
CAPC1608N | 4.7uF | CC_4.7uF_0603 | C4, C15, C17 | CAP CER 4.7uF X5R +-20% 10V 0603 | 3
CAPC1608L | 100nF | CC_100nF_0603 | C5, C6, C7, C8, C9, C10, C11, C12, C13, C14, C18, C20, C22, C23, C24, C28, C31, C32, C33, C34, C35, C36, C37, C38, C39, C40, C41 | CAP CER 100nF X7R +-10% 50V 0603 | 27
CAPC1608L | 10nF | CC_10nF_0603 | C19 | CAP CER 10nF X7R +-10% 50V 0603 | 1
CAPC3216L | 22uF | CC_22uF_1206 | C26, C27 | CAP CER 22uF Y5V -20% +80% 10V 1206 | 2
SMC | VS-30BQ015-M3/9AT | DS_VS-30BQ015-M3 | D1 | DIODE, SCHOTTKY, 3A, 15V, DO-214AB / SMC | 1
DIOM4227X23N | SS14-E3/5AT | DS_SS14E3 | D2, D3 | DIODE, SCHOTTKY, 1A, 40V, DO-214AC | 2
WL-SMCW0603 | Red | DL_150060RS75000 | DL1 | LED Red 250mcd 0603 SMD | 1
WL-SMCW0603 | Green | DL_150060GS75000 | DL2 | LED Green 430mcd 0603 SMD | 1
RESC3216N | 2A | FS_Fuse_2.0A | F1 | Fuse 2.0A Very Fast Acting 1206 SMD | 1
RESC3216N | 0.25A | FS_Fuse_0.25A | F2 | Fuse 0.25A Very Fast Acting 1206 SMD | 1
FCI_USB_10118194-0001LF | JS_USB_MICRO_B | JS_USB_MICRO_B_SMT | H1 | CONN USB MICRO B RECPT SMT R/A | 1
IDC2.54-V10D | Header 5X2 Vert | JA_HDR_IDC_5X2_VERT | H2 | IDC Header, 2,54mm, 10-Pin, Vert | 1
BATT_HEADER_3POS | Battery_HEADER_3pin | Battery_HEADER_3pin | H3 | 3Pin Header 2.54mm spacing Digikey #WM22663-ND | 1
MOLEX_KK_3_HDR | LED_Strip | LED_Strip_Header | H4 | CONN HEADER 3POS 2.54mm VERT_Thru Hole | 1
INDC3216L | 1A max, Idc 0.3R, | IN_Ferrite-Bead | L1, L3 | Ferrite Bead, Rdc 0.3R, Z100MHZ 600R, Imax 1A, SMD 1206 | 2
INDUCTOR5u2 | IND 5.2UH 6A | CDRH104RNP-5R2NC | L2 | FIXED IND 5.2UH 6A 22 MOHM SMD | 1
HDR1X2 | CH1 | JA_PIN_Header 2 | P2 | Header, 2-Pin | 1
HDR1X2 | CH2 | JA_PIN_Header 2 | P3 | Header, 2-Pin | 1
HDR1X2 | CH3 | JA_PIN_Header 2 | P4 | Header, 2-Pin | 1
HDR1X6 | GPIO_Header | JA_PIN_Header 6 | P5 | Header, 6-Pin | 1
HDR1X2 | CH4 | JA_PIN_Header 2 | P6 | Header, 2-Pin | 1
HDR1X2 | Joy_sel | JA_PIN_Header 2 | P7 | Header, 2-Pin | 1
HDR1X3 | Servo | JA_PIN_Header 3 | P8 | Header, 3-Pin | 1
BUZZER | Piezo Buzzer | Piezo Buzzer | P9 | TDK - PS1240P02BT - BUZZER, PIEZO, 70DB, 12.2MM | 1
HDR1X3 | LS1 | JA_PIN_Header 3 | P11 | Header, 3-Pin | 1
HDR1X3 | LS2 | JA_PIN_Header 3 | P12 | Header, 3-Pin | 1
HDR1X2 | Spare | JA_PIN_Header 2 | P13 | Header, 2-Pin | 1
SOT323_M | BC817W | TB_BC817W | Q1 | NPN GP Bipolar Transistor 45V 500mA SOT323 | 1
SOT23_L | SSM3J328R,LF | TM_SSM3J328R | Q2 | MOSFET P-CH 20V 6A SOT23-3 | 1
RESC1608L | 27K | RS_27K | R1 | RES 27K OHM 1/10W 5% 0603 SMD | 1
RESC1608N | 47K | RS_47K | R2 | RES 47.0K OHM 1/10W 5% 0603 SMD | 1
RESC1608L | 150K | RS_150K | R3 | RES 150K OHM 1/10W 5% 0603 SMD | 1
RESC1608L | 100K | RS_100K | R4, R31 | RES 100K OHM 1/10W 5% 0603 SMD | 2
RESC1608L | 3K | RS_3K | R5 | RES 3K OHM 1/10W 5% 0603 SMD | 1
RESC1608L | 2K | RS_2K | R6 | RES 2K OHM 1/10W 5% 0603 SMD | 1
RESC1608L | 27R | RS_27R | R8, R24 | RES 27 OHM 1/10W 5% 0603 SMD | 2
RESC1608L | 2K2 | RS_2K2 | R18, R19 | RES 2.2K OHM 1/10W 5% 0603 SMD | 2
RESC1608L | 1K | RS_1K | R21, R22 | RES 1.0K OHM 1/10W 5% 0603 SMD | 2
RESC3216L | 1R | RT_1R | R23 | RES 1R OHM 1/4W 5% 1206 SMD | 1
RESC1608L | 10K | RS_10K | R27, R34 | RES 10.0K OHM 1/10W 5% 0603 SMD | 2
RESC1608L | 24K | RS_24K | R29 | RES 24K OHM 1/10W 5% 0603 SMD | 1
EVQPNF05M | nRST | WS_EVQPNF05M | S1 | Panasonic 6 x 3.5mm SMD Light Touch Switch Type SMD | 1
EVQPNF05M | SLEEP | WS_EVQPNF05M | S2 | Panasonic 6 x 3.5mm SMD Light Touch Switch Type SMD | 1
LQFP64_L | ATSAM4S8BA-ANR | SE_ATSAM4S16BA-MU | U1 | IC MCU 32BIT 512KB FLASH 64LQFP | 1
SOT95P280X145-5N | CAT6219-330TDGT3 | SV_CAT6219-330TDGT3 | U2, U4 | IC REG LIN 3.3V 500MA TSOT23-5 | 2
RD_8_1 | ADP2302ARDZ-5.0 BUCK | ADP2302ARDZ-5.0-R7 | U3 | IC REG BUCK 5V 2A 8SOIC | 1
QUAD24 | MPU-9250 | MPU-9250 | U5 | 9 axis IMU | 1
SOT23-6_N | SN74LVC1T45 | SN74LVC1T45 | U7, U8, U9 | 1.8V - 5V level converter | 3
NRF24 | nRF24 SMD | NRF24 | U10 | nRF24 SMD Module | 1
Joystick_Sw | Joystick 10k with Sw | Joystick 10k with Sw | VR1 | JOYSTICK 10K OHM 2 AXIS TH | 1
6.0X3.5-4 | 12MHz | XT_CRYSTAL_12MHz_18pF | Y1 | CRYSTAL 12MHZ 18PF 6X3.5mm SMD | 1
 |  |  |  |  | 99
Approved |  | Notes

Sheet: Project Information
Project Full Path | C:\Users\angus\OneDrive - University of Canterbury\Uni\2022 3rd Pro\Semester 1\ENCE 461\wacky-racers\hw\Hat\Hat.PrjPcb
Project Filename | Hat.PrjPcb
Variant Name | None
Data-Source Filename | hat.PcbDoc
Data-Source Full Path | C:\Users\angus\OneDrive - University of Canterbury\Uni\2022 3rd Pro\Semester 1\ENCE 461\wacky-racers\hw\Hat\hat.PcbDoc
Title | Bill of Materials for PCB Document [hat.PcbDoc]
Total Quantity | 99
Report Time | 8:21 AM
Report Date | 22/04/2022
Report Date & Tine | 22/04/2022 8:21 AM
Output Name | Bill of Materials
Output Type | BOM_PartType
Output Generator Name | BOM
Output Generator Description | Bill of Materials

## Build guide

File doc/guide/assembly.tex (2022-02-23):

\chapter{PCB assembly}

\section{SMT lab induction}

You cannot use the SMT lab unless you have performed a lab induction.

\section{Solder pasting}

Solder paste needs to be applied to each pad.  Usually this is applied
using a stencil but for small boards, it can be applied using a
syringe.  The solder paste must be fresh.

\section{Component placement}

The components are placed onto the pasted pads using a pick-and-place
machine.  The key is to get the orientation of chips, diodes, and LEDs
correct.

It is easy to orient the MCU incorrectly.  The big dot \textbf{does
  not mark pin 1}\footnote{I think they add this to sell more
  chips\ldots}, see \reffig{pin1}.

\begin{figure}[!h]
  \centering
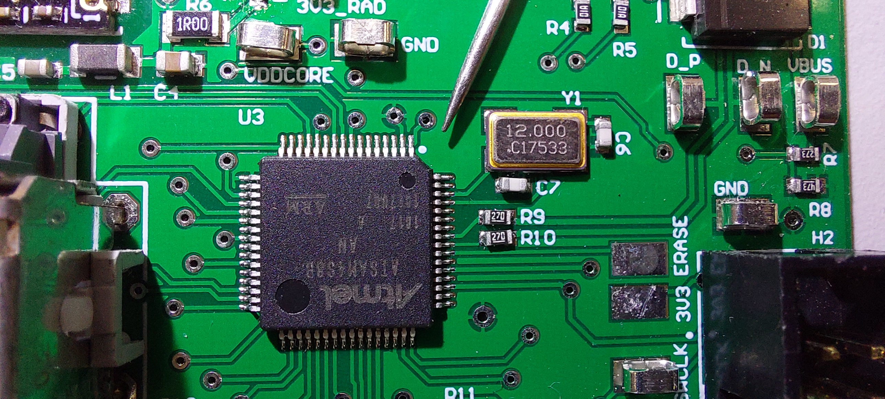
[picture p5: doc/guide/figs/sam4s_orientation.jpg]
  
  \caption{Pin 1 of the SAM4S is marked by the chamfer and the small
    dot.}
  \label{fig:pin1}
\end{figure}

\section{Reflow oven}

When the board has been populated, the PCB is placed in the reflow
oven.  Thus is preheated to 150$^{\circ}$ C so you must use oven gloves to
put your board in the oven.  At the end of the process, remove your
PCB using oven gloves.  You do not need to clean the board.

\section{Visual inspection}

Look for solder bridges, see \reffig{solder-bridge}, especially
between IC pins.  The bridges can be removed with a fine-tipped
soldering iron.

\begin{figure}[!h]
  \centering
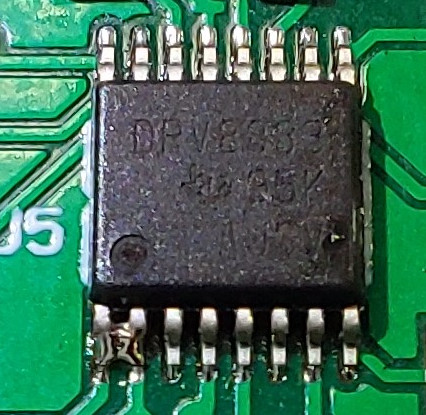
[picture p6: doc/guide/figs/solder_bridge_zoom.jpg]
  
  \caption{A solder bridge shorting pins 1 and 2 of the H-bridge.
    This can easily occur if there is too much solder paste.}
  \label{fig:solder-bridge}
\end{figure}

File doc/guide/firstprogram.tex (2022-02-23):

\chapter{First program}
\label{first-program}

Your first program to test your board should only flash an LED (the
hello world equivalent for embedded systems). The key to testing new
hardware is to have many programs that only do one simple task each.

Do not underestimate the effort required to flash your first LED. You
require:
%
\begin{itemize}
\item
  A computer with \program{git} installed and a useful shell program
  such as \program{bash}. UC has a
  \href{http://ucmirror.canterbury.ac.nz/}{mirror} for a variety of
  Linux distributions; we recommend Ubuntu or Mint.

\item A cloned copy of the Wacky Racers git repository, see
  \hyperref[project-cloning]{project cloning}.

\item
  A working ARM toolchain (arm-none-eabi-gcc/g++ version 4.9.3 or
  newer), see \hyperref[toolchain]{toolchain}.

\item
  An ST-link programmer and 10-wire ribbon cable for programming. You
  can get the adaptor from Scott Lloyd in the SMT lab. You will need
  to make your own cable (For a grey ribbon cable, align the red
  stripe with the small arrow denoting pin 1 on the connector. For a
  rainbow ribbon cable, connect the brown wire to pin 1.). There are
  two variants of the ST-link programmer with \textbf{different
  pinouts} so you may need to customise your programming cable.
\item
  Plenty of gumption.
\end{itemize}

Once you have a working toolchain and the source code installed:
%
\begin{enumerate}
\item Set up the PIO definitions for your board, see
  \hyperref[configuration]{configuration}.

\item Compile your program, see \hyperref[compilation]{compilation}.

\item See if your SAM4S is running, see \hyperref[openocd]{OpenOCD}.

\item Configure the SAM4s to boot from flash memory, see
  \hyperref[booting-from-flash-memory]{booting from flash memory}.

\item Program the SAM4s, see \hyperref[programming]{programming}.
\end{enumerate}

\begin{figure}
\input{figs/openocd.schtex}
\caption{How OpenOCD interacts with the debugger and the SAM4S.}
\label{fig:openocd diagram}
\end{figure}

\section{Connecting with OpenOCD}
\label{openocd}

\begin{figure}[!h]
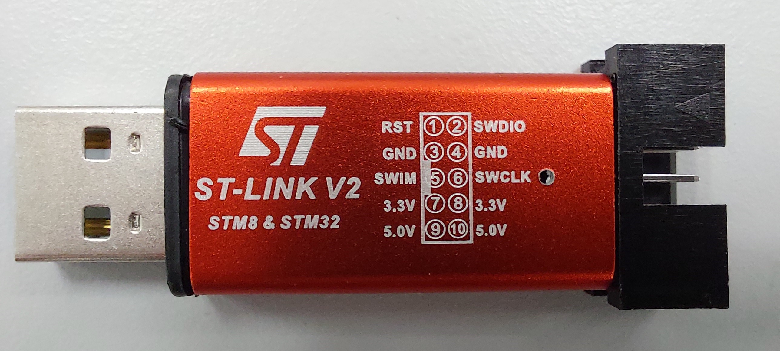
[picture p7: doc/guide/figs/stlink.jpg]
  \centering 
  \caption{A Chinese copy of a ST-link programmer.  Unfortunately, the
    manufacturer is not consistent with the pinout!}
  \label{fig:stlink}
\end{figure}

\program{OpenOCD} is used to program the SAM4S, see \reffig{openocd diagram}.

For this assignment, we use a ST-link programmer to connect to the
SAM4S using serial wire debug (SWD). This connects to your board with
a 10-wire ribbon cable and an IDC connector.

\begin{enumerate}
\item
  Before you start, disconnect the battery and other cables from your
  PCB.
\item
  Connect a 10-wire ribbon cable from the ST-link programmer to the
  programming header on your PCB. This will provide 3.3\,V to your
  board so your green power LED should light.
\item
  Open a \textbf{new terminal window, e.g., bash} and
  start \program{OpenOCD}.
\end{enumerate}

\begin{minted}{bash}
$ cd wacky-racers
$ openocd -f src/mat91lib/sam4s/scripts/sam4s_stlink.cfg
\end{minted}

All going well, the last line output from \program{OpenOCD} should be:

\begin{verbatim}
Info : sam4.cpu: hardware has 6 breakpoints, 4 watchpoints
\end{verbatim}

Congrats if you get this! It means you have correctly soldered your
SAM4S. If not, do not despair and do not remove your SAM4S. Instead,
see \protect\hyperref[troubleshooting]{troubleshooting}.

\section{LED flash program}
\label{led-flash-program}

For your first program, use
\wfile{test-apps/ledflash1/ledflash1.c}. The macros \code{LED1_PIO}
and \code{LED2_PIO} need to be defined in \file{target.h} (see
\protect\hyperref[configuration]{configuration}).

\inputminted{C}{../../src/test-apps/ledflash1/ledflash1.c}

The LED should flash at 2\,Hz.  If it does not, try the
\hyperref[pwm-test]{PWM test} program and check the frequency with an
oscilloscope.

\section{Configuration}
\label{configuration}

Each board has different PIO definitions and requires its own
configuration information. The \wfile{boards} directory contains a
configuration for the hat and one for the racer board.  \textbf{You
must edit these to customise your board.}  Each configuration
directory contains three files:

\begin{itemize}
\item
  \file{board.mk} is a makefile fragment that specifies the MCU model,
  optimisation level, etc.
\item
  \file{target.h} is a C header file that defines the PIO pins and
  clock speeds.
\item
  \file{config.h} is a C header file that wraps target.h. Its purpose
  is for porting to different compilers.
\end{itemize}

\textbf{You will need to edit the target.h file for your board} and set
the definitions appropriate for your hardware. Here's an excerpt from
\file{target.h} for a hat board:

\begin{minted}{C}
/* USB  */
#define USB_VBUS_PIO PA5_PIO

/* ADC  */
#define ADC_BATTERY PB3_PIO
#define ADC_JOYSTICK_X PB2_PIO
#define ADC_JOYSTICK_Y PB1_PIO

/* IMU  */
#define IMU_INT_PIO PA0_PIO

/* LEDs  */
#define LED1_PIO PA20_PIO
#define LED2_PIO PA23_PIO
\end{minted}

\section{Compilation}
\label{compilation}

Due to the many files required, compilation is performed using
makefiles.

The demo test programs are generic and you need to specify which board
you are compiling them for. The board configuration file can be chosen
dynamically by defining the environment variable \code{BOARD}. For
example:
%
\begin{minted}{bash}
$ cd src/test-apps/ledflash1
$ BOARD=racer make
\end{minted}

If all goes well, you should see at the end:
%
\begin{verbatim}
   text    data     bss     dec     hex filename
  11348	   2416	    176	  13940	   3674	ledflash1.bin
\end{verbatim}

To avoid having to specify the environment variable \code{BOARD}, you
can define it for the rest of your session using:
%
\begin{minted}{bash}
$ export BOARD=racer
\end{minted}
%
and then just use:
%
\begin{minted}{bash}
$ make
\end{minted}

\section{Booting from flash memory}
\label{booting-from-flash-memory}

By default the SAM4S runs a bootloader program stored in ROM. The SAM4S
needs to be configured to run your application from flash memory.

If \program{OpenOCD} is running you can do this with:

\begin{minted}{bash}
$ make bootflash
\end{minted}

Unless you force a complete erasure of the SAM4S flash memory by
connecting the \pin{ERASE} pin to 3.3\,V, you will not need to repeat
this command.

\section{Programming}
\label{programming}

If \program{OpenOCD} is running you can store your program in the flash
memory of the SAM4S using:

\begin{minted}{bash}
$ make program
\end{minted}

When this finishes, one of your LEDs should flash. If so, congrats! If
not, see \protect\hyperref[troubleshooting]{troubleshooting}.

To reset your SAM4S, you can use:
%
\begin{minted}{bash}
$ make reset
\end{minted}

\section{Makefiles}

Compilation is performed using makefiles, since each application
requires many files.  Rather than having large makefiles, a heirarchy
of makefile fragments is employed.  Dependencies are automatically
generated (so not all the files have to be recompiled each time).

A board description can be selected with the \code{BOARD} environment
variable.  This can be defined for each command, for example,
%
\begin{minted}{bash}
$ BOARD=racer make program
\end{minted}

Alternatively, this can be defined for a session:
%
\begin{minted}{bash}
$ export BOARD=racer
$ make program
\end{minted}

Each of the makefiles has the following phony targets:
%
\begin{description}
\item[all]  --- compile the application
\item[program] --- compile the application and download to the MCU (you need Openocd running)
\item[debug] --- start the debugger GDB (you need Openocd running)
\item[reset] --- reset the MCU (you need Openocd running)
\item[clean] --- delete the executable, object files, and dependency files.
\end{description}

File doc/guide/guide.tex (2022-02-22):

\documentclass[a4paper,11pt]{book}
\usepackage{lmodern}
\usepackage{circuitikz}
\usepackage{amssymb,amsmath}
\usepackage{siunitx}
\usepackage{ulem}

% use upquote if available, for straight quotes in verbatim environments
\IfFileExists{upquote.sty}{\usepackage{upquote}}{}

% use microtype if available
\IfFileExists{microtype.sty}{%
\usepackage[]{microtype}
\UseMicrotypeSet[protrusion]{basicmath} % disable protrusion for tt fonts
}{}

% This requires pdflatex -shell-escape
\usepackage{minted}

\usepackage[colorinlistoftodos]{todonotes}
\newcommand{\mtodo}{\todo[inline]}

\PassOptionsToPackage{hyphens}{url} % url is loaded by hyperref
\usepackage[unicode=true]{hyperref}
\hypersetup{pdfborder={0 0 0},
  breaklinks=true}

\hypersetup{colorlinks=true, linkcolor=blue, urlcolor=blue, citecolor=green}

\urlstyle{same}  % don't use monospace font for urls
\usepackage{graphicx,grffile}
\makeatletter
\def\maxwidth{\ifdim\Gin@nat@width>\linewidth\linewidth\else\Gin@nat@width\fi}
\def\maxheight{\ifdim\Gin@nat@height>\textheight\textheight\else\Gin@nat@height\fi}
\makeatother

% Scale images if necessary, so that they will not overflow the page
% margins by default, and it is still possible to overwrite the defaults
% using explicit options in \includegraphics[width, height, ...]{}
\setkeys{Gin}{width=\maxwidth,height=\maxheight,keepaspectratio}
\IfFileExists{parskip.sty}{%
\usepackage{parskip}
}{% else
\setlength{\parindent}{0pt}
\setlength{\parskip}{6pt plus 2pt minus 1pt}
}

\setlength{\oddsidemargin}{0mm}
\setlength{\evensidemargin}{-14mm}
\setlength{\marginparwidth}{0cm}
\setlength{\marginparsep}{0cm}
\setlength{\topmargin}{2mm}
\setlength{\textwidth}{168mm}
\setlength{\textheight}{240mm}
\setlength{\footskip}{10mm}

\setlength{\emergencystretch}{3em}  % prevent overfull lines
\providecommand{\tightlist}{%
  \setlength{\itemsep}{0pt}\setlength{\parskip}{0pt}}

%\setcounter{secnumdepth}{0}

% Redefines (sub)paragraphs to behave more like sections
\ifx\paragraph\undefined\else
\let\oldparagraph\paragraph
\renewcommand{\paragraph}[1]{\oldparagraph{#1}\mbox{}}
\fi
\ifx\subparagraph\undefined\else
\let\oldsubparagraph\subparagraph
\renewcommand{\subparagraph}[1]{\oldsubparagraph{#1}\mbox{}}
\fi

% set default figure placement to htbp
\makeatletter
\def\fps@figure{htbp}
\makeatother

\newcommand{\program}[1]{\texttt{#1}}
\newcommand{\code}[1]{\mintinline{C}{#1}}
\newcommand{\file}[1]{\texttt{#1}}
\newcommand{\wfile}[1]{\href{https://eng-git.canterbury.ac.nz/wacky-racers/wacky-racers/-/blob/master/src/#1}{\mintinline{bash}{wacky-racers/src/#1}}}
\newcommand{\wikiref}[2]{\href{http://ecewiki.elec.canterbury.ac.nz/mediawiki/index.php/#1}{\mintinline{bash}{#2}}}
\newcommand{\pin}[1]{\texttt{#1}}
\newcommand{\sig}[1]{\texttt{#1}}
\newcommand{\ud}{\mathrm{d}}                    % upright d (derivative)

\newcommand{\reffig}[1]{\mbox{Figure~\ref{fig:#1}}}
\newcommand{\reftab}[1]{\mbox{Table~\ref{tab:#1}}}
\newcommand{\refeqn}[1]{\mbox{(\ref{eqn:#1})}}

\title{The Wacky Racers Guide, V1.010}
\author{Michael Hayes and Mutley}
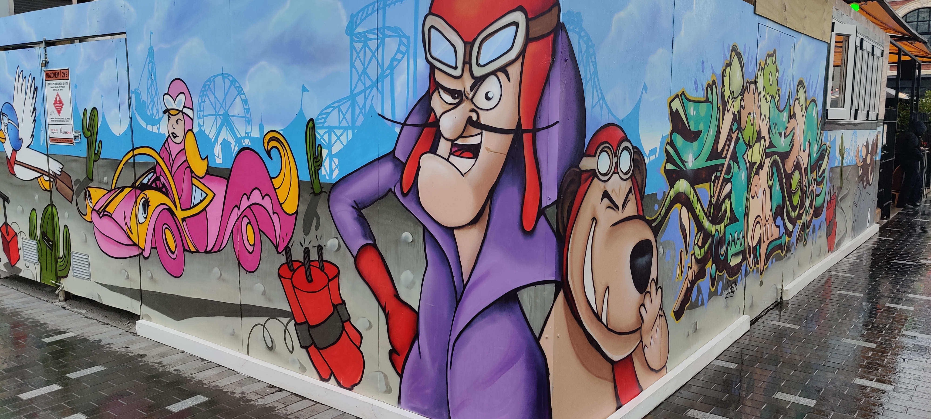
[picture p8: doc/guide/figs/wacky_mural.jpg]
\date{\today\\[2cm] }

\begin{document}
\maketitle

\tableofcontents

%\input{requirements}
%\input{schedule}
\input{introduction}
\input{hardware}
\input{schematic}
\input{PCB}
\input{assembly}
\input{software}
\input{firstprogram}
\input{testprograms}
\input{application}
\input{libraries}
\input{troubleshooting}
\input{rework}
\input{debugging}

\appendix
\input{openocd}
\input{git}
\input{sleeping}
\input{EMC}
\input{pins}
%\input{assessment}

\end{document}

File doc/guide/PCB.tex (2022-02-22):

\chapter{PCB layout}

Before you lay out your PCB, an hour spent checking your schematic
will avoid many hours of testing and rework grief!  I annotate a
printed schematic with a highlighter to ensure I have considered
everything.

\section{Altium tutorial}

The Altium tutorial for creating a PCB can be found on the ENCE461
Learn page.

\label{pcb-recommendations}

\section{Placement}
\label{placement}

\begin{enumerate}
\item
  Keep small signal analogue components (radio) well away from digital
  electronics and power electronics.
\item
  Place local decoupling capacitors to minimise the loop area.
\item
  Place bulk capacitors close to where power comes from.
\item
  Keep the crystal close to the MCU.
\item
  Place switches so they can be pushed.
\item
  Place LEDs so they can be seen.
\item
  Place USB connector so it can be connected to.
\item
  Place connectors on edge of PCB with wires going away from the board.
\end{enumerate}

\section{Power supplies}

\begin{enumerate}

\item Use planes for power distribution.

\item If cannot use power plane for power connection, make trace as
  wide\footnote{To reduce inductance and resistance.} as possible.

\item Do not put splits in planes\footnote{Unless you know what you
  are doing.}.

\item Keep planes away from the radio antenna; otherwise the radio
  range is limited.

\item Before `pouring' a polygon to create a power or ground plane
  connect the nets with tracks and vias.
\end{enumerate}

\section{Signal traces}

\begin{enumerate}

\item
  Use microstrips for any signal above 50\,kHz.

\item
  Keep signal traces apart to reduce crosstalk (3-W rule).

\item
  Avoid signal traces jumping layers (especially for signals above
  50\,kHz).  If you do, use vias close to ends of traces.

\item
  Use tented\footnote{These have a layer of insulating solder resist.}
  vias under components with metal pads.

\end{enumerate}

\section{Recommended layouts}

For any switching power supply, sensitive analogue, or BGA fanout, the
chip manufacturer usually provides a recommended layout.

\section{Check list}
\label{PCB-check-list}

\begin{enumerate}
\item Check your schematic.  Then get someone else to check your
  schematic.  Query every component.

\item Perform a DRC (Design Rule Check)].

\item Add PCB test points, test points, and more test points.  You
  will need one for every signal and power supply.  \textbf{You have
    been warned!}  If you don't believe me, compare the size of an
  oscilloscope probe to a surface mount IC pin and see if you can hold
  the probe in place.  I recommend using 1206 test points since the
  smaller ones rip off easily.

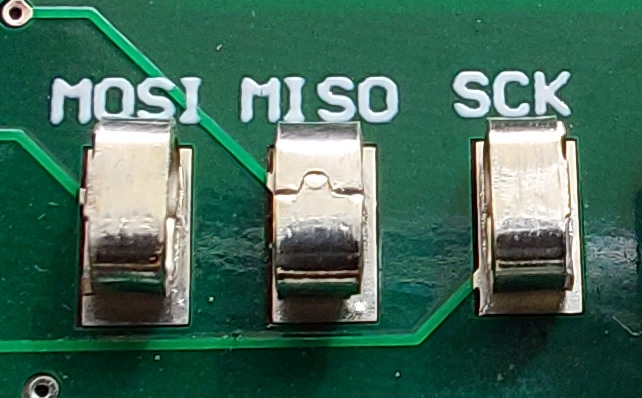
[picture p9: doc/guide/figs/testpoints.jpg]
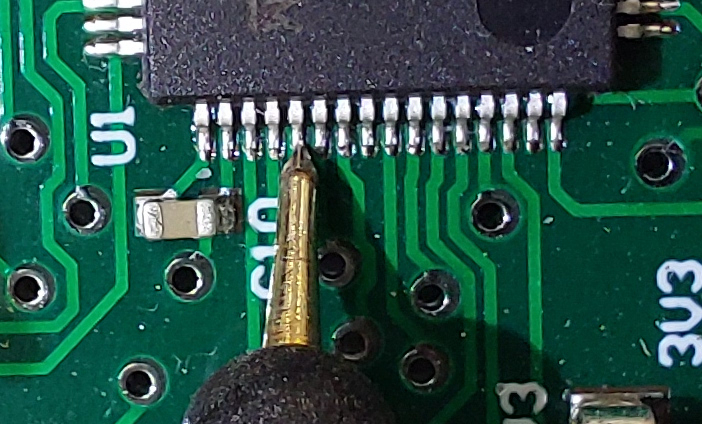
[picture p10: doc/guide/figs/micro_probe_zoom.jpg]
    

\item Label the test points on the silk screen with meaningful names.

\item Add ground test points that you can clip an oscilloscope ground
  lead to.  Keep these away from other test points to avoid shorting
  with the oscilloscope ground clip.

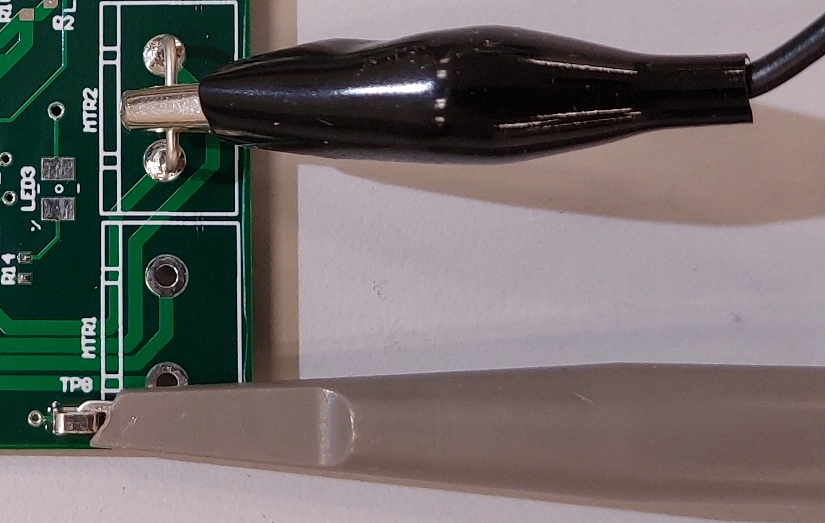
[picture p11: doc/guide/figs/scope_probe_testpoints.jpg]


\item Check mounting holes.

\item Check component footprints, especially connectors, voltage
  regulators, and surface mount transistors by placing the parts on a
  print-out of the PCB design.

\item Ensure that power supply traces are wide as possible, preferably
  planes, to reduce their inductance.

\item Ensure that high current traces are wide as possible to reduce their resistance.

\item Do not connect IC pins directly between the pads since it is not
  possible to tell if a solder blob is accidental or deliberate.

\item Insert vias to ground plane to ensure that all parts are connected.  Do not leave unconnected copper.

\item If not using plated through vias do not place vias under
  components.

\item If placing vias under components with exposed metal pads, make
  sure the vias are ``tented'' (covered in solder mask) to prevent
  unexpected shorts.

\item Stitch power or ground planes where vias or tracks cut them up.

\item If a track is of width W it should be separated from the next
  track by a width 2W to reduce crosstalk.  This is the 3-W rule since
  the track centres are 3W.  An exception is for differential signals;
  these should be routed close together with a uniform spacing.

\item Do not run a microstrip traces right on the edge of the PCB.  If
  track is of width W it should be at least W from the edge to reduce
  electric field fringing effects.

\item Use large traces for pads on connectors that may be subject to
  mechanical forces (power jacks, pluggable terminals, etc.) to
  prevent trace cracking.

\item If you have high voltages check clearances.

\item Check pad to track clearances to avoid potential solder bridges.

\item Check that it is possible to top-solder through-hole components
  on non-plated-through boards.

\item Ensure like signals are grouped, data lines, address lines, control lines, analogue signals, etc.

\item Check the thermal path for parts that get hot.

\item Run tracks over reference (power or ground) planes to create a
  microstrip trace; avoid tracks running over cuts in a reference
  plane.

\item Check that hole diameters are larger than the pin diameters for
  connectors and through hole. 25\% over the lead diameters is
  typical.  Remember to look at the diagonal dimension for square pins
  or your holes may be too small.

\item Check the drill file report to make sure the hole sizes are what
  you would expect. There should be no holes with sizes of zero, no
  weird sizes, no super large sizes unless required by the design.

\item Check that connections of thermal vias have clearance to other
  traces and pads.

\item Pay close attention to clearances on internal planes of
  multilayer boards; shorts on these planes can only be removed with
  precision drilling.

\item Number pins on connectors, big ICs, selection jumpers, etc. For
  connectors, number enough pins that pin ordering is obvious. For
  large ICs consider adding tickmarks every 5 pins.

\item Make the pad for pin 1 of every IC square. Also consider putting
  a silkscreen dot next to pin 1.

\item Leave at least 20--50\,mils (0.5--1.3\,mm) clearance between
  components and the edge of the board. This makes it less likely that
  inaccuracies in board fabrication will cause part of a pad to get
  chopped off.

\item Check for component clearances from enclosure including heights.

\item Look at each net individually to ensure that it doesn't take an
  overly long path around the board. Many layout tools have a
  highlight net feature that makes this a fast process.

\item Don't let the silkscreen overlap pads. Try to avoid having
  silkscreen overlapping via holes or areas of the board that will be
  routed away (large holes, slots, tabs, etc.), since legibility will
  be poor.

\item If ICs are being soldered with solder paste ensure that there is
  a solder mask between pads.
 \end{enumerate}

\section{Design rule checks}

This section considers common Altium design rule violations.  For more
information see the Altium wiki.

\subsection{PCB manufacture violations}

You do not want any of these.  If a trace is too thin then etching may
produce a hole in it.  It two traces are too close together, they may
end up joined.

\subsection{PCB assembly violations}

\subsubsection{SMD neck-down constraint}

Traces connecting to SMD pads often need to be reduced in thickness to
minimise heat transfer from the SMD pad (unequal PAD temperatures can
lead to component tombstoning or rotation in the oven).  The traces
widths should be a maximum of 50 \% of the width of the pad and should
be of the same size to prevent component movement due to unequal pad
temperatures.  The length of the neck-down can be as short as 0.5\,mm.

This is not so critical for integrated circuits with many pins (except
if a solder mask is not used since solder might flow away from the
pad).

\subsubsection{Silk to solder mask}

Here Altium thinks the silk screen is being printed over a pad; most
manufacturers detect this and delete the offending text.

\subsubsection{Minimum solder mask sliver constraint}

This occurs with chips having pins that are close together.  It is a
warning that the PCB manufacturer may not be able to make the thin
sliver of solder mask that is applied between pads to reduce the
chances of having a solder blob between the pins.  For a prototype it
is not a concern since the solder blob can be easily removed with a
small soldering iron.

\subsection{Signal integrity violations}

\subsubsection{SMD pad to plane constraint}

What this means is that you have placed a via to a power or ground
plane too far from a SMD pad.  Simply add another via closer to the
pad.  There is no need to skimp on vias for power supply connections.

This violation indicates you that you are adding unnecessary
inductance by increasing the loop area and thus compromising signal
integrity.

Unfortunately, Altium does not detect when you use a power decoupling
capacitor to mitigate this inductance and thus will report
false-positives.  For some reason, whenever there is a decoupling
capacitor pad between an IC pad and a via to a plane, it cannot
calculate the distance of the trace and reports it as being about
2.3\,m!  So, ignore this error.

The goal is to place the decoupling capacitor to minimise the area of
the loop formed by the current flowing from the capacitor to the IC
power and ground pins.  Multiple vias to power/ground planes should
then be placed on the other side of the capacitor.

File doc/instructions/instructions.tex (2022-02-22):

\documentclass[11pt, a4paper]{article}
\title{Wacky Racers 2022 Instructions}
\author{Michael Hayes}
\date{Version 1.1, \today}

\usepackage[margin=1in]{geometry}
\usepackage{parskip}
\usepackage{float}
\usepackage{todonotes}
\presetkeys{todonotes}{inline}{}
\usepackage{graphicx}
\usepackage[T1]{fontenc}
\usepackage{makecell}
\usepackage[breaklinks=true]{hyperref}
\usepackage{tabularx}
\usepackage{subcaption}
\usepackage{listings}
\usepackage{siunitx}
\usepackage{circuitikz}
\usepackage{tikz}
\usetikzlibrary{arrows}

\newcommand{\code}[1]{\texttt{#1}}

\newcommand{\danielemail}{\url{mailto:daniel.morris@pg.canterbury.ac.nz}}
\newcommand{\scottemail}{\url{mailto:scott.lloyd@.canterbury.ac.nz}}
\newcommand{\diegoemail}{\url{mailto:diego.ramirez@canterbury.ac.nz}}

\newcommand{\daniel}{\href{mailto:daniel.morris@pg.canterbury.ac.nz}{Daniel Morris}}
\newcommand{\scott}{\href{mailto:scott.lloyd@.canterbury.ac.nz}{Scott Lloyd}}
\newcommand{\diego}{\href{mailto:diego.ramirez@canterbury.ac.nz}{Diego Ramirez}}

\newcommand{\theguide}{\href{https://eng-git.canterbury.ac.nz/wacky-racers/wacky-racers/-/blob/master/doc/guide/guide.pdf}{The Wacky Racers Guide}}

\begin{document}
\maketitle

\section{Introduction}

The purpose of this assignment is to design, build, and program an
embedded system using an ARM microcontroller and surface mount
technology.

The goal for each group of four students is to build a remote
controlled vehicle (the Wacky Racer) and its controller (the Wacky
Hat).  At the conclusion of the assignment there will be a dastardly race!

Each group is comprised of two sub-groups of two students.  One of
these subgroups constructs the Wacky Racer and the other constructs
the Wacky Hat.  You may be asking why is the Wacky Hat called the
Wacky Hat?  Well, a hat that controls a remote vehicle using head
motions is not an ordinary hat!

\section{Requirements}

The following requirements are mandatory if you wish to maximise your
marks.

\subsection{Wacky racer}

\begin{enumerate}
\item The chassis is to be constructed by each group.  These can be 3-D printed,
  constructed from Perspex or wood, etc.  A standard chassis is available from
  the Electronics Lab technician (Diego Ramirez).  The electronics must be
  visible on top of the chassis.
\item Have a standard working bump sensor (supplied).
\item Locomotion can only use two 6\,V DC motors (supplied).
\item Everything must be powered from a single 5-cell NiMH battery pack (supplied).
\item Use a single four layer printed circuit board of dimension 85\,mm$\times$64\,mm.
\item Use an ARM microcontroller (Atmel SAM4S8).
\item Drive the motors using H-bridges (Texas Instruments DRV8833 dual
  H-bridge is recommended).
\item Regulate the nominal battery voltage to 5\,V with a buck
  regulator IC (ADP2302ARDZ-50).
\item Be decorated with an LED tape (supplied) controlled by the MCU.
\item Use a USB interface for debugging.
\item Use a serial wire debug interface for MCU programming/debugging.
\item Have adequate battery fusing and reverse polarity protection.
\item Have a sleep pushbutton to enter low-power mode.
\item If the battery voltage drops below 5\,V, an LED should flash and high power draw devices should be disabled.
\item Have an active-high red LED to indicate errors.
\item Have an active-high green LED to indicate status.
\item Interface to the Wacky Hat with a Nordic nRF24 SMD radio module.
\item Have four jumper selectable radio channels.
%\item Have a mounted RFID card (supplied) that can be read by the Wacky ramps.
\item Be humorous.
\end{enumerate}

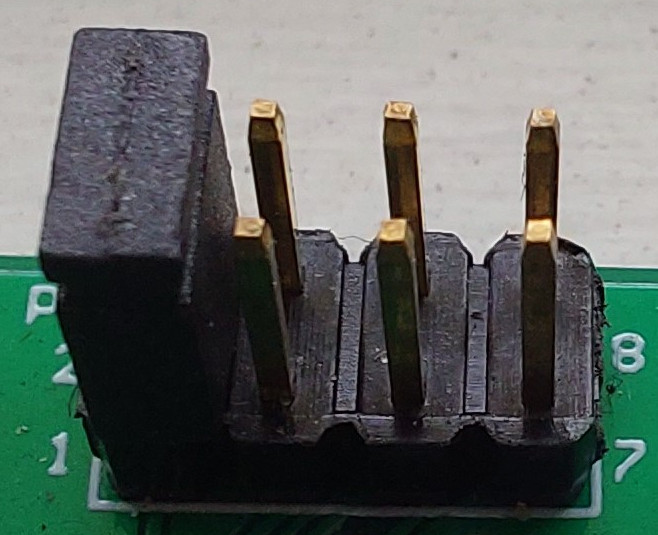
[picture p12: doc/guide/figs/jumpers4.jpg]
\hspace{120mm}

Each Wacky Racer can have a dastardly means of hindering another
team's Wacky Racer.  However, you cannot:
%
\begin{itemize}
\item Damage or destroy another Wacky racer (except in the battle royale)
\item Damage the venue
\item Injure a spectator
\item Jam the radio signals
\end{itemize}

\vspace{1cm}

\begin{figure}[h]
    \centering
    \input{racer_top_level.tex}
    \caption{Racer board top level diagram.}
\end{figure}

\vfill\pagebreak

\subsection{Wacky hat}

\begin{enumerate}
\item Construct a Wacky Hat that contains all the electronics.
\item Everything must be powered from a single 5-cell NiMH battery pack (supplied).
\item Have adequate battery fusing and reverse polarity protection.
\item Use a single four layer printed circuit board of dimension 85\,mm$\times$64\,mm.
\item Use an ARM microcontroller (Atmel SAM4S8).
\item Regulate the nominal 6\,V battery voltage to 5\,V with a buck
  regulator IC (ADP2302ARDZ-50).
\item Be decorated with an LED tape (supplied) controlled by the MCU.
\item Use an I2C IMU (MPU-9250) for head motion detection.
\item Use a USB interface for debugging.
\item Use a serial wire debug interface for MCU programming/debugging.
\item Have a joystick in case the IMU does not work.
\item Have a sleep pushbutton to enter low-power mode.
\item If the battery voltage drops below 5\,V, an LED should flash and high power draw devices should be disabled.
\item Have an active-high red LED to indicate errors.
\item Have an active-high green LED to indicate status.
\item Play sound when the bumper is hit.
\item Interface to the Wacky Racer with a Nordic nRF24 SMD radio module.
\item Have four jumper selectable radio channels.
\item Be humorous.
\end{enumerate}

%\vspace{1cm}

\begin{figure}[h]
  \centering
  \input{hat_top_level.tex}
  \caption{Racer hat top level diagram.}
\end{figure}

\vfill\pagebreak

\section{Assignment schedule}

The planned activities for the timetabled labs in the Embedded Systems
Lab (ESL) are:
%
\begin{flushleft}
  \begin{tabular}{ c l l }
    Week            &  Assistance  &  Assessment \\
    \hline \hline
    T1-1 & Altium tutorial 1 (schematics)  & \\
    T1-2 & Altium help      & Schematic submission for review (Friday 5pm) \\
    T1-3 & Schematic review & \\
    T1-4 & Altium tutorial 2 (PCB) &          \\
    T1-5 & Altium help      & PCB submission 1    \\
    T1-6 & Altium help      & PCB submission 2    \\
    T1-7 & General          &                   \\
    \hline
    B-1  & (break)          &                   \\
    B-2  & (break)          &                   \\
    B-3  & (break)          &                   \\
    \hline
    T2-1 & General          & Blinky            \\
    T2-2 & General          & IMU/motors        \\
    T2-3 & General          & Radio control     \\
    T2-4 & General          & Functionality     \\
    T2-5 & Competition      & Competition, critique  \\
  \end{tabular}
\end{flushleft}

Notes:
%
\begin{enumerate}
\item There are two lab streams.  Your group will need to sign up to
  one of the streams.  Choose a group between 1--19 for the Tuesday
  stream or group 20--39 for the Wednesday stream.

\item There there may be a 6--10 day delay for the PCBs to be
  manufactured from the time of submission.  You will then need to
  book an assembly session in the SMT lab provided you have done the
  SMT lab induction.

\item Do not underestimate the blinky milestone.  It requires having a
  functional PCB, a functional toolchain, and the ability to download
  code into the microcontroller's flash memory.

\end{enumerate}

\section{Assessment}

The marks breakdown (max. 0x64) is:
%
\begin{flushleft}
  \begin{tabular}{ll}
    PCB submission & 0--0xa marks\\
    Blinky milestone  & 0x5 marks\\
    IMU/motor milestone  & 0x5 marks\\
    Radio control milestone  & 0x5 marks\\
    Functional assessment & 0--0x14 marks \\
    Board inspection & 0--0x1e marks \\
    Competition & 0--0xa marks \\
    Individual critique & 0--0xf marks \\
  \end{tabular}

\end{flushleft}

\subsection{Milestones}

There are five milestones.  To achieve the associated marks, they must
be demonstrated to a T.A. by the end of the lab for your allotted
stream.  If you need an exception to this, see \daniel\ with a
\emph{very} good reason.  The milestone requirements are:
%
\begin{description}
\item [Schematic review] Submit your A3 schematic on Learn for
  review.  Lose 10 marks if you miss the submission time.

\item [PCB submission] Submit your PCB design to Learn for
  manufacture.  To encourage early submission there is a sliding scale
  for marks depending on when the PCB is submitted, see table.  After
  week 6, there is a 10 mark penalty per week.  \textbf{NB, a rushed
    PCB design will cause you more grief, more PCB rework, and a lower
    mark for the inspection.}

  \begin{tabular}{llll}
    Week & Submission day & Cut-off time  & Mark \\ \hline
    5    & Monday       & 1.00 pm & 10 \\
    5    & Tuesday      & 1.00 pm & 9 \\
    5    & Wednesday    & 1.00 pm & 8 \\
    5    & Thursday     & 1.00 pm & 7 \\
    5    & Friday       & 1.00 pm & 6 \\
    6    & Monday       & 1.00 pm & 5 \\
    6    & Tuesday      & 1.00 pm & 4 \\
    6    & Wednesday    & 1.00 pm & 3 \\
    6    & Thursday     & 1.00 pm & 2 \\
    6    & Friday       & 1.00 pm & 1  \\
  \end{tabular}

\item [Blinky] Demonstrate that can blink an LED controlled by the SAM4S.

\item [IMU/motors] For the Wacky Hat, demonstrate output of IMU
  readings to a PC using USB CDC.  For the Wacky Racer, demonstrate
  control of the motors from a PC using USB CDC.

\item[Radio control] Demonstrate sending commands from the Wacky Hat
  to the Wacky Racer over a radio link.
\end{description}

\textbf{If you cannot show the functionality of a previous milestone
  during any assessment, you will fail that assessment and loose any
  marks from the previous milestone.}

\subsection{Functionality assessment}

Functionality requirements:
%
\begin{flushleft}
  \begin{tabular}{l|l}
    Wacky racer & Wacky hat \\ \hline \hline
    Blink LED                      & Blink LED \\
    Drives LED tape                & Drives LED tape \\
    Drive motors forward/backward  & Read from IMU \\
    Speed control of motors        & Calculate speeds from IMU \\
    Steering control               & Joystick control \\
    Receive radio message          & Send radio message \\
    Jumper selectable radio channel & Jumper selectable radio channel  \\
    Dies on bump                   & Plays sound on bump \\
    Low voltage indication         & Low voltage indication \\
  \end{tabular}
\end{flushleft}
%
Marks are allocated on how well things work.  Up to 5 bonus marks can
be awarded for extra functionality such as:
%
\begin{flushleft}
  \begin{tabular}{l|l}
    Wacky racer                & Wacky hat \\ \hline \hline
    Dastardly stuff            & Plays interesting sounds \\
    Sleep mode                 & Sleep mode \\
  \end{tabular}
\end{flushleft}

Sleep mode is where you shutdown the MCU to save energy and use a
pushbutton to awake the MCU via an interrupt.  Is is easy to get wrong
and hard to save every microamp.

\subsection{Competition}

The competition is a race around an obstacle course.  Marks will be
awarded every time you pass over a Wacky Ramp in the correct order.

%These ramps have an RFID card reader that will detect your Racer if
%you have correctly fitted an RFID card.  The Wacky Ramps change colour
%when they detect a Wacky Racer.

To be awarded any marks for the race:
%
\begin{enumerate}
\item Your vehicle must stop for at least 5\,s if the bumper is hit.

\item Your vehicle must be controlled by motions of the Wacky hat
  sitting on someone's head.
\end{enumerate}

After the races, there will be a battle royale where the last
operational wacky racer wins.  Hitting the bumper of an opponents
wacky racer removes them from the battle.

Marks will also be awarded for wackiness, group costumes, etc.

\subsection{PCB inspection}

This is assessed after the competition.  The categories are:
%
\begin{enumerate}
\item Layout (component placement etc.)
\item Construction (tidiness, rework, etc.)
\item Testability
\item Power supplies (routing, decoupling, etc.)
\end{enumerate}

\vfill\pagebreak
\section{Schedule}

\begin{description}
\item [Week~1]\mbox{}\\[-0.4cm]

  \begin{itemize}
  \item Form a group of four and register your group on Learn.  If you
    cannot form a group of 4, contact \daniel.

  \item Read the Requirements section in this document.

  \item Read the System Design section in the \theguide.

  \item Attend Altium schematic tutorial.

  \end{itemize}

\item [Week~2]\mbox{}\\[-0.4cm]

  \begin{itemize}
  \item Start your schematic design.

  \item Peruse the datasheets of the key components.

%  \item Sign-up for a SMT lab induction
  \end{itemize}

\item [Week~3]\mbox{}\\[-0.4cm]

  \begin{itemize}
  \item Submit your Altium schematic for review.

  \item Attend review feedback session.
  \end{itemize}

\item [Week~4]\mbox{}\\[-0.4cm]

  \begin{itemize}
  \item Attend Altium PCB tutorial.

  \item Start your PCB layout.
  \end{itemize}

\item [Week~5]\mbox{}\\[-0.4cm]

  \begin{itemize}
  \item Watch SMT lab induction video.

  \item Submit PCB design (early round).
  \end{itemize}

\item [Week~6]\mbox{}\\[-0.4cm]

  \begin{itemize}
  \item Submit PCB design (late round).
  \end{itemize}

%\item [Week~7]\mbox{}\\[-0.4cm]

%\item [Week~8]\mbox{}\\[-0.4cm]

\item [Week~9]\mbox{}\\[-0.4cm]

  \begin{itemize}
  \item Populate and test PCB.
  \end{itemize}

\item [Week~10]\mbox{}\\[-0.4cm]

  \begin{itemize}
  \item Populate and test PCB.
  \item Demonstrate blinky program.
  \end{itemize}

\item [Week~11]\mbox{}\\[-0.4cm]

  \begin{itemize}
  \item Demonstrate blinky program.
  \end{itemize}

\item [Week~12]\mbox{}\\[-0.4cm]

  \begin{itemize}
  \item Demonstrate IMU/motors functionality.
  \end{itemize}

\item [Week~13]\mbox{}\\[-0.4cm]

  \begin{itemize}
  \item Demonstrate radio control.

  \item Plan your costumes!
  \end{itemize}

\item [Week~14]\mbox{}\\[-0.4cm]

  \begin{itemize}
  \item Demonstrate full functionality.

  \item Prepare your costumes and dastardly stuff!
  \end{itemize}

\item [Week~15]\mbox{}\\[-0.4cm]

  \begin{itemize}
  \item Practice control of your wacky racer.
  \item Attend wacky race.
  \item Submit PCB for inspection (box in SMT lab).
  \item Return chassis, batteries, and ST-link programmers.
  \item Submit individual critique to Learn.
  \end{itemize}

\end{description}

\section{Technical stuff}

Read this section carefully.  There are clues as to how we mark your PCBs.

\subsection{Version control}

Use version control for everything, or else!  Learning git is
frustrating but is a skill you will not regret, see \theguide\ for
details.

Your group leader should create a forked copy of the wacky-racers git project
and then add the other group members to the project.  This can be done by:

\begin{enumerate}
\item Go to \url{https://eng-git.canterbury.ac.nz/wacky-racers/wacky-racers}

\item Click `Fork' button.  This will create a copy of the main repository for the project.

\item Click on the `Settings' menu then click the `Expand' button for
`Sharing and permissions'.  Change `Project Visibility' to `Private'.

\item Click on the `Members' menu and add group members as Developers.

\item Using a bash terminal (or other useful shell), enter the command:

\lstset{language=bash}
\lstset{basicstyle=\ttfamily\small}
\lstset{keywordstyle=\color{black}\ttfamily}
\lstset{breaklines}

\begin{lstlisting}
  $ git clone https://eng-git.canterbury.ac.nz/your-userid/wacky-racers.git
\end{lstlisting}

If you do not want to have to enter your password for every git
push/pull operation, you should set up ssh-keys and use the git URL instead:

\begin{lstlisting}[breaklines]
  $ git clone git@eng-git.canterbury.ac.nz:your-userid/wacky-racers.git
\end{lstlisting}

\item Add a remote URL for the main repository.
%
\begin{lstlisting}[breaklines]
  $ cd wacky-racers
  $ git remote add upstream https://eng-git.canterbury.ac.nz/wacky-racers/wacky-racers.git
\end{lstlisting}
%
Again if you do not want to manually enter your password, you can use:
%
\begin{lstlisting}[breaklines]
  $ cd wacky-racers
  $ git remote add upstream git@eng-git.canterbury.ac.nz:wacky-racers/wacky-racers.git
\end{lstlisting}

\item If we add more demo code or tweak the instructions in the main
repository, you can get the updated stuff using:
%
\begin{lstlisting}[breaklines]
  $ git pull upstream master
\end{lstlisting}
\end{enumerate}

\subsection{Schematics}

\begin{enumerate}
\item Read the Altium tutorial on Learn.

\item Read the \theguide.

\item Add you and your partner's name and your group number to the
  title block.

\item Save PDF files of your schematics in your source repository.
  \textbf{Note, when debugging your PCBs, we will not help you until
    you show us your printed A3 schematic}.

\item I bet that you will not have enough test points to clip an
  oscilloscope probe to.  Do not think you can hold the probe tip
  against an MCU pin without shorting something.  Ensure you give a
  meaningful name to the test point in its comment field.

    

\item Ground test points are essential for an oscilloscope earth clip.
  A U-shaped piece of wire soldered into two holes is good for this.
  Keep ground test points clear of other test points since the earth
  clip may short between them.  You will probably require at least two
  ground points on opposite sides of the PCB.



\item Checking the schematic is the most crucial part of the
  assignment.  If the schematic is wrong then your PCB will be wrong
  and you will need to do rework.  So, schematics must be thoroughly
  checked by another person.

%% \item Consider fall-back options if you have a problem with your PCB.

%%   The IMU for the Wacky Hat is tiny and we \textbf{strongly recommend} that you
%%   provide an alternative connector for connecting the following IMU module:
%%   \href{https://www.aliexpress.com/item/SPI-IIC-MPU9250-MPU-9250-MPU-9250-9-Axis-Attitude-Gyro-Accelerator-Magnetometer-Sensor-Module-MPU9250/32216818498.html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}{MPU-9250 on AliExpress}

%%   Similarly for the Wacky Racer, in case the H-bridge fails, provide two
%%   three-pin servo connectors so that external Electronic Speed
%%   Controllers (ESC) can be used to drive the motors.

\item It would be useful to have a jumpers connected to PIO pins so
  that you can configure your board.  For example, if a jumper is in,
  use the joystick, otherwise use the IMU.

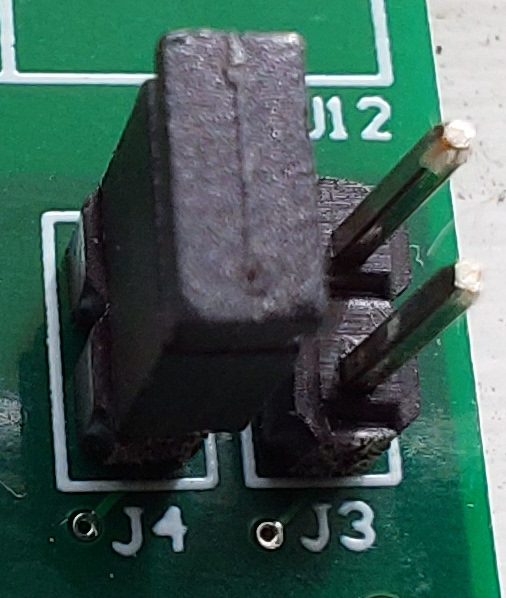
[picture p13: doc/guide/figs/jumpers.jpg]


\item In case you forget something, I suggest running some spare PIO
  pins from the MCU to some pads or a connector.

\end{enumerate}

\subsection{PCBs}

\begin{enumerate}
\item Your four-layer PCBs are going to be manufactured in batches.
  There is at least a week turnaround time to get the boards made.

\item It is important that you check footprints for parts they you
  create.  We will impose a 10\% penalty for each rerun of a PCB, say
  due to a footprint mistake.  Get your partner to check.

\item In Altium, turn off the test point designators and turn on
  comments instead. This lets you give them human readable names to
  make your lives easier.

\item PCB layouts must be thoroughly checked by another person.

\item A PCB track can blow faster than a fuse. So keep high current
  tracks fat and short.

\item Clearly mark the positive and negative battery connections on
  the silk screen.

\item Some of the chips can get hot so thermal considerations are
  required.  Follow the manufacturers' guidelines in the datasheets.

\item The switching regulators can interfere with the radios.

\item Use a design rule check to see if any of the following
  constraints are violated:
%
\begin{itemize}
\item Minimum trace width (0.15\,mm)
\item Minimum trace clearance (0.15\,mm)
\item Minimum via size (0.3\,mm hole, 0.6\,mm outer diameter)
\item Minimum hole size (0.3\,mm)
\item Minimum annular ring (0.1\,mm)
\end{itemize}
%
For every violation of one these rules, we will deduct 1\% from your
final mark.

\item Check the checklist in the \theguide\ before submission.
\end{enumerate}

\subsection{Assembly}

\begin{enumerate}
\item Finding shorts is extremely frustrating so maximise clearances
  and test for shorts before populating components.

\item Components can be put through the oven on the reverse side
  although heavy components may need to be glued.

\item Never assume where pin 1 is on an IC; check the datasheet.
  5--10\% of groups will get this wrong.

\end{enumerate}

\subsection{Software}

\begin{enumerate}
\item Read the \theguide.

\item If you are not using version control, you are foolish.

\item Inspect MPH's sample code.

\item If you are trying to program the SAM4S for the first time and
  are feeling tired or impatient, then do something else.
\end{enumerate}

\subsection{Debugging}

\begin{enumerate}
\item Start running small programs (such as the provided demo
  programs) to test each feature separately.

\item An oscilloscope is your friend.

\item It is possible to use the GDB debugger but you need to know what
  you are doing, especially with optimised code.

\item Drawing a diagram of what you think is happening is highly
  recommended. A simple circuit diagram or timing diagram will often
  help you realise what you have missed and let you fix it without
  asking for help.

\end{enumerate}

\subsection{Possibly asked questions with answers}

\begin{itemize}
\item \emph{Why use the SAM4s MCU?}  For this application most MCUs
  would suffice, even an 8-bit AVR microcontroller.  To level the
  playing field, I have chosen a MCU most students would not have used
  before.  This is an ARM based MCU made by Atmel I have used this in
  a number of projects.  Indeed we used to teach this chip in ENCE361.
  There are many other similar MCUs made by different manufacturers
  such as the STM32 that would just as suitable.

\item \emph{Why use a four layer PCB?}  Come to lectures to find out!

\item \emph{Why use 7.2\,V NiMH batteries for the Wacky Racers?}
  These were a legacy of previous Wacky Racers.  They are also safer
  than lithium batteries with sleep-deprived students.

%% \item \emph{Why can't I program my device using Windows?} Due to
%%   various aspects of the Windows ecosystem, setting up a fully
%%   functional build environment is more complicated, will often vary
%%   from machine to machine, will often break filepaths, and will often
%%   cause bizarre compilation errors. Use at your own risk, we will not
%%   assist in debugging issues related to Windows.

\end{itemize}

\section{Assistance}

\daniel\ (\danielemail) is in charge of the assignment with support
from the technicians \scott\ (\scottemail) and \diego\ (\diegoemail),
and a team of teaching assistants.

\begin{itemize}
\item Emails to the lecturers (except of a personal nature) will be
  quietly ignored.

\item If you have a generic question, please use the ENCE461 Learn
  discussion page.  Note, under the advanced options you can send your
  post without a 30\,minute delay.

\item All decisions regarding legality of your dastardly devices are
  at the whim of \daniel.  Email \daniel\ if you wish to keep your
  ideas secret.

\item TAs will be available in the scheduled lab times.  Priority will
  be given to groups assigned to the current lab session. \textbf{We
    will only provide assistance to students who have a printed A3
    schematic sheet in front of them and have already tried looking up
    the problem in the \theguide.}

\item For questions pertaining to Altium, surface mount assembly, and
  surface mount rework, see \scott\ (SMT Lab technician) and
  \diego\ (Electronics Lab technician).

\item Michael Hayes is really busy pulling all the string behind the
  scenes and so will only help with gnarly problems referred to by
  \daniel!

\end{itemize}

\section{COVID}

\begin{itemize}
\item Some of the lab sessions may need to be held online.

\item The first term does not need lab access, however, you will need
  to be able to run Altium remotely or run the free student-edition of
  Altium.  The instructions and files can be found on the ENCE461
  Learn page.

\item If because of illness or isolation your group cannot meet a
  milestone, email \daniel.

\item Some of the milestones may need to be altered.

\end{itemize}

\end{document}

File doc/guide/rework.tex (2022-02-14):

\chapter{Rework}
\label{rework}

Flux is your friend when doing rework.  However, you need to remove it
from your board when finished, see \hyperref[flux removal]{flux
  removal}.  You should check all rework with a magnifier and look for
solder bridges.

\section{Removing resistors and capacitors}

\begin{enumerate}
\item Apply flux from syringe to pads.

\item Use tweezer soldering iron.
\end{enumerate}

\section{Removing larger parts}

\begin{enumerate}
\item Apply flux from syringe to pads.

\item Use a grunty soldering iron.  \textbf{Do not push hard with a
  small soldering iron since this will bend the tips.}
\end{enumerate}

\section{Removing MCU}

\begin{enumerate}
\item Only remove as last resort.

\item Apply flux from syringe to all pins.

\item Get Scott to show you how to use the hot-air gun.  The key is to
  choose a head that matches the size of the MCU and getting the
  temperature correct.

\item Be careful not to lift pads or tracks.
\end{enumerate}

\section{Adding a wire}

\begin{enumerate}
\item For a signal trace, choose the very fine wire.

\item Cut to length and strip insulation from both ends.  The second
  end is a lot harder!

\item Bend wire to shape and tape down to the PCB.  Note, you can run
  this wire through vias.

\item Apply flux from syringe to both pads.

\item Use small soldering iron to solder wires in place.
\end{enumerate}

\section{Flux removal}
\label{flux removal}

\begin{enumerate}
\item Scrub board with using flux-cleaner and brush.
\item Clean board with a towel.
\item Wash board with a little bit of IPA.
\item Clean board with a towel.
\end{enumerate}

\mtodo{Show photos of clean board and dirty board}

\begin{figure}[!h]
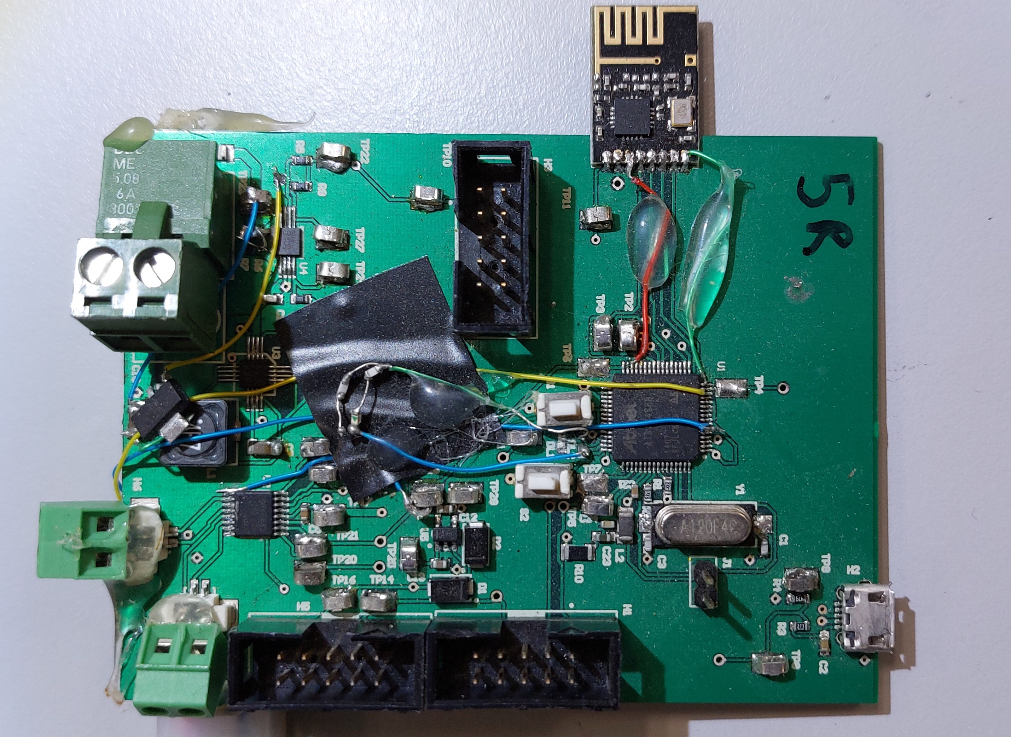
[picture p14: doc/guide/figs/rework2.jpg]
  \centering 
  \caption{Example of a PCB where not much care was taken with the
    schematic resulting in a lot of rework. The board worked!}
  \label{fig:rework2}
\end{figure}

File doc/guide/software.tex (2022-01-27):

\chapter{Software installation}
\label{software}

\section{Git}

Your group leader should fork the Wacky Racers project template.  This
creates your own group copy of the project on the eng-git server that
you can modify, add members, etc.

Each group member then clones the group project.

\subsection{Project forking}
\label{project-forking}

The template software is hosted on the eng-git \program{Git} server.
To fork the template:

\begin{enumerate}
\item
  Go to \url{https://eng-git.canterbury.ac.nz/wacky-racers/wacky-racers}.
\item
  Click the `Fork' button. This will create a copy of the main repository
  for the project.
\item
  Click on the `Settings' menu then click the `Expand' button for
  `Sharing and permissions'. Change `Project Visibility' to `Private'.
\item
  Click on the `Members' menu and add group members as Developers.
\end{enumerate}

\subsection{Project cloning}
\label{project-cloning}

Once your project has been forked from the template project, each group
member needs to clone it. This makes a local copy of your project on
your computer.

If you are using an ECE computer, it is advised that you clone the
project on to a removable USB flash drive. This will make git
operations and compilation 100 times faster than using the networked
file system.

There are two ways to clone the project. If you are impatient and do not
mind having to enter a username and password for every git pull and push
operation use:
%
\begin{minted}[breaklines]{bash}
$ git clone https://eng-git.canterbury.ac.nz/groupleader-userid/wacky-racers.git
\end{minted}

Otherwise, set up \program{ssh-keys} and use:
%
\begin{minted}[breaklines]{bash}
$ git clone git@eng-git.canterbury.ac.nz:groupleader-userid/wacky-racers.git
\end{minted}

You can have several different cloned copies of your project in
different directories. Sometimes if you feel that the world,
and \program{git} in particular, is against you, clone a new copy,
using:
%
\begin{minted}[breaklines]{bash}
$ git clone https://eng-git.canterbury.ac.nz/groupleader-userid/wacky-racers.git wacky-racers-new
\end{minted}

\section{Toolchain}
\label{toolchain}

The toolchain comprises the compiler, linker, debugger, C-libraries,
and OpenOCD.

The toolchain is installed on computers in the ESL and CAE. It should
run under both Linux and Windows.  If there is a problem ask the
technical staff.

The toolchain can be downloaded for Windows, Linux, and macOS from
\url{https://developer.arm.com/tools-and-software/open-source-software/developer-tools/gnu-toolchain/gnu-rm/downloads}.
For Linux and macOS, however, it is better to install the toolchain using your
system's package manager: see the instructions in the following subsections.

\subsection{Toolchain for Linux}

First, if using Ubuntu or Mint, ensure the latest versions are
downloaded:
%
\begin{minted}{bash}
$ sudo apt update && sudo apt upgrade
\end{minted}

Then, install the compiler:
%
\begin{minted}{bash}
$ sudo apt install gcc-arm-none-eabi
\end{minted}

Install the C and C++ libraries:
%
\begin{minted}{bash}
$ sudo apt install libnewlib-arm-none-eabi libstdc++-arm-none-eabi-newlib
\end{minted}

Install the debugger, GDB:
%
\begin{minted}{bash}
$ sudo apt install gdb-multiarch
\end{minted}

Install OpenOCD:
%
\begin{minted}{bash}
$ sudo apt install openocd
\end{minted}

\subsection{Toolchain for macOS}

For macOS machines that have \href{https://brew.sh}{homebrew}
installed, you can use the following command:

\begin{minted}{bash}
$ brew install openocd git
$ brew cask install gcc-arm-embedded
\end{minted}

\section{IDE}

I am content with using the command-line and emacs as a text editor
but I guess that you are not.  If you are familiar with geany I
suggest that you use that.  If you want bells and whistles, I suggest
using Visual Studio Code.  While it is written by Microsoft, it is
free and runs on Windows, Linux and macOS.

\subsection{Visual Studio Code}

VS Code is a modern and highly versatile text editor.  With the right
extensions, it can be used to develop code for just about anything!
This project has been configured for VS Code on the ESL computers (but
its relatively easy to modify it to work on a home computer, be it
Windows, Linux, or Mac). For the simplest use, simply go \code{File ->
Open Folder} and point it at the wacky-racers repository.  This will
give you access to the build tools (Ctrl-Shift-B) that have been
setup. These must be run from inside a program (i.e., ledflash1.c).
Finally, opening a program and pressing F5 will launch a debugging
session that will allow the use of breakpoints and variable
inspection.

When building your programs, the \code{BOARD} configuration variable
must be set. In VS Code this is done by choosing your C++
configuration (bottom right of the window) which by default will be
either hat or racer.

As a side note, the compilation and debugging requires the
installation of two VS Code extensions:
%
\begin{enumerate}
\item C/C++ (Microsoft)
\item Native Debug (Web Freak)
\end{enumerate}
%
VS Code should automatically prompt you to install these when you open
  the wacky-racers directory.

\section{Using Windows in the ESL}

On the Windows machines in the ESL, the toolchain is located at
\file{C:\textbackslash{}ence461\textbackslash{}tool-chain}. This needs to be
added to your session's \code{PATH} variable so toolchain commands can be run
without needing to specify their full path. See
\wikiref{ARM-GCC_in_the_DSL}{ARM-GCC in the DSL} on ECEWiki for more
information.

You can use Windows Command Prompt similarly to a Linux Shell. To open, press
\code{Windows Key} + \code{R}, type \code{cmd}, and \code{Enter}. Then run
\file{C:\textbackslash{}ence461\textbackslash{}tool-chain} inside the CMD window
to source the toolchain. Although this guide is written for the Linux shell, the
commands will also work in Command Prompt provided you observe the following
differences:
\begin{itemize}
\item To change between drives (e.g. \file{C:} and \file{D:}), pass the
\code{/d} switch to the \code{cd} command.
\item Instead of \code{export VARIABLE=value}, use \code{set VARIABLE=value}.
Also you cannot set an environment variable when you run a command, so
\code{BOARD=hat make} won't work; run \code{set BOARD=hat} and \code{make} in
separate commands instead.
\item To run GDB, you must invoke the complete command name
\code{arm-none-eabi-gdb}.
\item In path names, \file{/} is replaced by \file{\textbackslash} (backslash).
\end{itemize}

If you are using Windows on the ESL machines and want to use VS Code, you can
run \file{vscode.bat} located in the top level of the \file{wacky-racers}
repository. This will open VS Code with the repository added to the workspace
and the necessary toolchain added to \code{PATH}.

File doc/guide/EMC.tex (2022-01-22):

\chapter{EMC}

Electromagnetic emission (EMI) occurs with changing electric and
magnetic fields.  A good PCB design should have good electromagnetic
compatibility (EMC); this means that it has low EMI and that is has
low susceptibility to changing electric and magnetic fields.

\section{Electromagnetic coupling}

It is worth recapping the fundamental equations.  A changing aggressor
current, $i_a(t)$, flowing around a loop induces a
voltage\footnote{This voltage magically appears around a loop and does
  not obey Kirchhoff's voltage law.  It will mostly `appear' across
  the highest resistance in the loop.} in a victim loop according to
Faraday's law,
%
\begin{equation}
  v_v(t) = M \frac{\ud i_a(t)}{\ud t},
\end{equation}
%
where $M$ is the mutual inductance.  The mutual inductance depends on
the areas of the aggressor and victim loops and their orientation.  It
is minimised by using microstrips.

A changing aggressor voltage induces a current in a victim circuit
according to
%
\begin{equation}
  i_v(t) = C \frac{\ud v_a(t)}{\ud t},
\end{equation}
%
where $C$ is the mutual capacitance that depends on the separation
between the traces and the distance the traces run beside each other.
From Ohm's law, the victim current will produce a voltage $i_v(t) R$
across a resistance $R$.  Thus low resistance circuits are more immune
to capacitive coupling.

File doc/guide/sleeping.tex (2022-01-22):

\chapter{Sleeping}

Sleeping a MCU is important for embedded systems applications to
prolong battery life.

\section{Dynamic power consumption}

The dynamic power consumption for CMOS is
%
\begin{equation}
  P = f C V^2,
  \label{eqn:power}
\end{equation}
%
where $f$ is the clock frequency, $C$ is the total switched
capacitance, and $V$ is the power supply voltage.  It can be difficult
to reduce $V$ for a MCU and so the power consumption can only be
reduced by lowering the clock frequency, $f$, and/or shutting down
parts of the MCU to reduce $C$.

\section{Slowing the CPU clock}

The SAM4S, like many MCUs, can be clocked from a number of sources.
For example, it has a slow clock generated by an RC oscillator with a
frequency of 32768\,Hz.

With the mat91lib library the slow clock can be selected using:
%
\begin{minted}{C}
    mcu_select_slowclock ();
\end{minted}

\textbf{Warning}, switching to a slow CPU clock will cause havoc with
OpenOCD.  You might not be able to load a new program.  In this case,
you will need to \hyperref[erasing-flash-memory]{erase flash memory}.

\section{Disabling the CPU clock}

Further power reduction can be achieved by disabling the CPU clock.
In effect, this reduces $C$ in \refeqn{power}.  The clock is disabled
using the ARM WFI (wait for interrupt) instruction.  The clock remains
disabled until an interrupt occurs.  The WFI instruction is executed
by calling the mat91lib \code{cpu_wfi ()} function, defined as:
%
\begin{minted}{C}
static inline void
cpu_wfi (void)
{
    __asm__ ("\twfi");
}
\end{minted}

\textbf{Warning}, before executing the WFI instruction, it is necessary
to enable an interrupt to wake the CPU.

\textbf{Warning}, disabling the CPU clock will cause havoc with
OpenOCD.

\section{Disabling peripherals}

Further power reduction can be achieved by shutting down peripherals
that are not required.  This also reduces $C$ in \refeqn{power}.  The
drivers in mat91lib have a shutdown function, e.g., \code{spi_shutdown
  ()}.

\section{Current measurement}

Measuring the current to determine power consumption is not
straightforward.  Usually, the voltage drop across a known resistance
is measured.  For normal operation, this resistance needs a low value
otherwise there will be significant voltage drop and the MCU will not
run.  When sleeping, a much larger resistor is required so that the
voltage drop can be measured (all going well the MCU will only take a
few microamps when sleeping).  One approach is to use two voltage drop
resistors connected in parallel when the MCU is running normally, and
to switch out the low value one when the MCU is sleeping.  There are
special current measuring devices that dynamically vary the voltage
drop resistor.

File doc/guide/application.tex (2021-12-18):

\chapter{Application}

Here are my recommendations for your Hat or Racer application:
%
\begin{enumerate}
\item Build and test your programs incrementally.

\item Write separate test programs that you can run when your
  application fails to work.  When debugging embedded systems, it is
  much easier to use a small test program rather than a large
  application.

\item It is easier to use a paced loop and poll the peripherals than
  using interrupts.

\item Disable the \hyperref[watchdog-timer]{watchdog timer} until you
  have robust code.
  
\end{enumerate}

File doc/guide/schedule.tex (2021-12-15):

\chapter{Schedule}

\begin{description}
\item [Week~1]\mbox{}\\

  \begin{itemize}
  \item Form a group of four and register your group on Learn.
  %\item Read the \hyperref[requirements]{requirements section}.
  \item Read the requirements section in the instructions document.
  \item Peruse the datasheets of the key components.
  \end{itemize}
  
\item [Week~2]\mbox{}\\
  
  \begin{itemize}
  \item Attend Altium schematic tutorial.
  \item Start your schematic design.
  \item Read suggestions in \hyperref[hardware]{hardware section}.
  \end{itemize}
  
\item [Week~3]\mbox{}\\
  
  \begin{itemize}
  \item Submit you Altium schematic for review.
  \item Attend review feedback session.
  \end{itemize}
  
\item [Week~4]\mbox{}\\
  
  \begin{itemize}
  \item Attend Altium PCB tutorial.
  \item Start your PCB layout.
  \end{itemize}

\item [Week~5]\mbox{}\\
  
  \begin{itemize}
  \item Attend SMT lab induction.
  \item Submit PCB design (early round).
  \end{itemize}

\item [Week~6]\mbox{}\\  
  
  \begin{itemize}
  \item Submit PCB design (late round).
  \end{itemize}

\item [Week~7]\mbox{}\\

\item [Week~8]\mbox{}\\  
  
\item [Week~9]\mbox{}\\
  
  \begin{itemize}
  \item Populate and test PCB.
  \end{itemize}  

\item [Week~10]\mbox{}\\

  \begin{itemize}
  \item Populate and test PCB.
  \item Demonstrate blinky program.
  \end{itemize}

\item [Week~11]\mbox{}\\  

  \begin{itemize}
  \item Demonstrate blinky program.
  \end{itemize}  
 
\item [Week~12]\mbox{}\\
  
  \begin{itemize}
  \item Demonstrate IMU/motors functionality.
  \end{itemize}
  
\item [Week~13]\mbox{}\\  
  
  \begin{itemize}
  \item Demonstrate radio control.
  \end{itemize}  
  
\item [Week~14]\mbox{}\\
  
  \begin{itemize}
  \item Demonstrate full functionality.
  \item Plan your costumes!
  \end{itemize}
  
\item [Week~15]\mbox{}\\
  
  \begin{itemize}
  \item Practice control of you wacky racer.
  \item Attend wacky race.
  \item Submit PCB for inspection (box in SMT lab).
  \item Return chassis and batteries.
  \item Submit individual critique to Learn.    
  \end{itemize}
  
\end{description}

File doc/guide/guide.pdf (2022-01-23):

## Mutley’s Guide To The Wacky Racers, V.013E-3

Michael Hayes

2021

2

# Contents

1 Introduction | 7
2 System design | 9
3 Schematic | 15
4 PCB layout | 17

3

4 | CONTENTS
5 PCB assembly | 23
6 Software installation | 25
7 First program | 29
8 Test programs | 35
9 Application | 47
10 Libraries | 49

CONTENTS | 5
11 Troubleshooting | 53
12 Rework | 63
13 Debugging | 65
A OpenOCD | 67
B Git | 69
C Sleeping | 71

6 | CONTENTS
D EMC | 73
E PIO pins | 75

# Chapter 1

# Introduction

This guide is written in the hope that it will ease your introduction into building, programming, and troubleshooting an embedded system. Making embedded systems is not easy; you have to get a lot right. One incorrect bit can be the difference between a working and a non-working system.

If you find things a little Linux-centric, well that’s the only operating system I’ve run for over twenty-five years. It is a common operating system for many high-end embedded systems; it runs on Android phones and probably on your internet router. And, yeah, I like the command-line; it is faster than using a mouse and GUI.

I would like to thank all those who have helped with this assignment over the years: Andrew Bainbrige-Smith, Blair Bonnett, Chris Cameron, Mike Cusdin, Matthew Edwards, Michael Frampton, Jay Gunathailake, Daniel Hopkins, Harry Mander, Daniel Morris, Morgan King, Scott Lloyd, Ben Mitchell, Diego Ramirez, Andre Renaud, Sam Spekreijse, Steve Weddell.

7

8 | CHAPTER 1. INTRODUCTION

# Chapter 2

# System design

The system requirements are specified in the assignment instructions.

## 2.1 Recommendations

1. Independently fuse the buck converter and H-bridge. This allows a fuse to be removed to isolate part of the circuit when finding a fault, such as a short across the power rails.
2. Have a zener diode to protect against overvoltage when your group member inadvertently cranks up the voltage from the bench power supply.
3. Have current limiting resistors for all off-board signals.
4. Have plenty of testpoints, especially for power supplies and signals. You will never have enough!
5. Have at least one grunty ground testpoint for attaching a scope ground clip.
6. Have a dedicated PIO pin to drive a testpoint that you can use to trigger an oscilloscope for debugging.
7. Have the SAM4S erase pin connected to a test point close to a 3.3 V testpoint. This is useful to completely erase the SAM4S flash memory when nothing works.
8. Have a MOSFET or servo interface for controlling something dastardly!

## 2.2 SAM4S MCU

The SAM4S MCU is overkill for this assignment but is typical of ARM processors used for bare-metal applications. The particular chip we are using is the SAM4S8B. This was made by Atmel and is now owned by Microchip. The datasheet is available at https://www.microchip.com/en-us/product/ATSAM4S8B. (https://www.microchip.com/en-us/product/ATSAM4S8B)

The SAM4S8B has a 32-bit ARM Cortex M4 RISC CPU that can run at 120 MHz and has 512 KB of flash memory and 128 KB of SRAM.

9

10 | CHAPTER 2. SYSTEM DESIGN

### 2.2.1 Power pins

The SAM4S has four grounds. They must all be connected. There are also seven power pins. These must all be connected since they power different parts of the chip. Note, some pins require 3.3 V while others require 1.2 V. The 1.2 V is generated by an internal voltage regulator.

### 2.2.2 Peripheral pins

Many of the peripheral pins are dedicated and cannot be reassigned in software, e.g., SPI, TWI, and USB pins. Note, there are restrictions on the PWM pins. See Table 11-2 in the SAM4S datasheet for the pin assignments. Also see PIO pins for electrical characteristics.

By default the PB4 and PB5 pins are configured for the JTAG debugger. These can be used for general PIO after setting an internal bit. See disabling JTAG pins.

The logic levels are set by the voltage on the VDDIO pin (usually 3.3 V). PA12–PA14 and PA26– PA31 can sink/source 4 mA. The USB pins (PB10–PB11) can sink/source 30 mA. The rest can only sink/source 2 mA of current.

The pullup and pulldown resistors are typically 100 kΩ. On reset, pullup resistors are enabled.

### 2.2.3 USART/UART

The SAM4S has two USARTs and two UARTs. The USARTs can emulate a UART, have hardware flow control, and have a better driver so they are recommended if you need a UART interface.

### 2.2.4 PWM

The SAM4S can generate four independent PWM signals. There are restrictions on which SAM4S pins they come out on. Note, the PWMLx and PWMHx signals are complementary (i.e., one is low while the other is high).

### 2.2.5 TWI

The SAM4S has two TWI peripherals (that can act as a master and a slave) with dedicated TWD and TWCK pins. External pull-up resistors are required. TWI1 shares pins with JTAG; you will need to disable JTAG in software.

### 2.2.6 SPI

The SAM4S has a single SPI peripheral with dedicated SCK, MISO, and MOSI pins. Any PIO pin can be used for the chip select¹

1For high speed operation (not needed for this assignment), you should use one of the dedicated chip select pins.

2.3. OTHER CHIPS | 11

### 2.2.7 ADC

The SAM4S has a single ADC with a multiplexer to select one of a number of analogue inputs. It can sample at 1 MHz.

### 2.2.8 USB

The SAM4S has a single USB peripheral connected to the DDP and DDM pins. 27 ohm series termination resistors are required, placed close to the SAM4S.

## 2.3 Other chips

### 2.3.1 DRV8833 dual H-bridge

The H-bridge has four modes: forward, reverse, slow decay (brake), and fast decay (coast). With slow decay mode, the motor is shorted so that it stops faster. With fast decay mode, the motor is open-circuited and so it takes longer to stop. However, there is little difference in practice, due to friction in the gearbox.

If you want control over fast decay and slow decay in both forward and reverse you will need four independent PWM signals. The SAM4S can provide four independent PWM signals but be careful since PWMxH and PWMxL are complementary signals driven from the same PWM source.

If you are clever, you can drive the H-bridge with only two PWM channels. If you are not so clever, you will have fast decay in one direction and slow decay in the other.

The capacitor connected to the bootstrap pin must be rated for 16 V. The datasheet recommends an X7R dielectric.

### 2.3.2 NRF24L01+ radio

The nRF24 module we provide is actually a tiny PCB with all of the high frequency analogue components populated for you. This module breaks out the SPI communication pins, the power supply pins, and two signal pins that you will need to connect to your microcontroller. The CE and IRQ pins can both go to general PIO pins while the SPI pins (MOSI, MISO, SCLK, CSN) need to be connected to the SAM4S SPI peripheral.

As this radio is ultimately an analogue circuit and any noise on the power supply can affect the signal quality, we recommend using a separate 3V3 regulator and using a low pass filter to provide the best power. Instead of a resistor, a ferrite bead is better.

You cannot have a PCB plane near the antenna of the radio otherwise the range will be severely limited.

The radio operates around 2.4 GHz and has 128 programmable channels, each of 1 MHz. Note, some of these channels use the same spectrum as Bluetooth and WiFi. A 5 byte address is appended to the start of each transmission and the receiver will only respond when the address matches.

The radio interfaces to the SAM4S using the SPI bus. The IRQ pin is driven low to indicate a packet has been received.

12 | CHAPTER 2. SYSTEM DESIGN

3.3 V

1 Ω

10 µF

GND

VCC

GND

nRF24

Figure 2.1: Power supply filtering; a ferrite bead is better than a resistor.

### 2.3.3 MPU9250 IMU

This contains a three axis accelerometer, a three axis gyroscope, and a three axis magnetometer. It appears that the magnetometer has been bolted on to the accelerometers/gyroscopes and requires more hoop jumping in software to make it work.,

It has two different I2C addresses (0x68 and Ox69) depending on the state of the AD0 pin.

### 2.3.4 Buck converter

The buck converter is a switch-mode regulator that converts the battery voltages to 5 V DC.

### 2.3.5 Voltage regulators

There are many flavours of voltage regulator. (http://ecewiki.elec.canterbury.ac.nz/mediawiki/index.php/voltage_regulators) Some are better for digital applications, some are better for analogue applications, some are better for low power applications, etc.

If you are using a voltage regulator with an enable pin, do not forget to allow for the time for the output voltage to ramp up. This can be tens of milliseconds depending on the capacitive load and current draw.

Note, some regulators have pins that you must not connect. Some have multiple pins for the same purpose; these must all be connected.

## 2.4 External components

### 2.4.1 Battery

The Wacky Racer batteries are Turnigy 5-cell 6 V, 2300 mAh, NiMH with a three pin JST connector. To preserve the battery life it is imperative to not draw current when the battery voltage is below 5 V. Note, when fully charged, the battery voltage may be 7.5 V.

The battery uses a standard RC servo connector: 3 pin 0.1” (pin 1 GND, pin 2 5V, pin 3 NC). We suggest connecting both the first and third pins to ground to allow the battery to be plugged in in both orientations. The 461 Altium library has a component named ‘Battery HEADER 3pin’ that is suitable to use.

2.4. EXTERNAL COMPONENTS | 13

### 2.4.2 LED Tape

The LED tape is a daisy-chained string of WS2812 LEDs. These LEDs use a clever mechanism to pass the RGB data down the string with different pulse lengths for 1 and 0. They are connected as shown in Figure 2.4.2.

5 V

GND

DIN | DIN | DOUT | DIN | DOUT | DIN | DOUT
| | VCC | | VCC | | VCC
GND | GND | GND

This means you will need to provide a three pin header (0.1” standard header) with the pinout: pin 1 5 V, pin 2 signal, pin 3 ground. Each individual LED has a maximum supply current of 60 mA (20 mA per red, green, blue channel). We will provide up to half a metre of LED tape to each car or hat, giving a maximum number of 30 LEDs to be driven.

### 2.4.3 Bumper

The provided bumper senses the contact through a simple limit switch. This switch is normally open and on contact will close.

3.3 V

limit switch

Note that the pullup resistor shown could simply be the internal pullup resistor on a PIO pin. The connector for the limit switch should be a simple 2 pin 0.1” header.

### 2.4.4 Buzzer

The buzzers supplied are passive piezo-electric devices. Applying a voltage across the two terminals causes the element to deform. Applying an alternating current to the device generates an audible tone. The larger the applied voltage differential, the louder the tone becomes. There are plenty of example circuits for piezo buzzers available online. Note, you need to be able to charge and discharge the capacitance of the pizeocrystal.

14 | CHAPTER 2. SYSTEM DESIGN

### 2.4.5 Motors

The motors available in the provided chassis are 6 V DC motors. These have a low DC resistance and will take as much current as the DRV8833 motor driver can supply. You need to add connectors for the motors, either 2 pin 0.1” headers or screw terminals are suggested.

### 2.4.6 Connectors

1. USB micro or mini connector for debugging
2. 3 pin 0.1” for LED tape (pin 1 5 V, pin 2 signal, pin 3 ground)
3. 2 pin 0.1” for bumper (pin 1 switch, pin 2 ground)
4. 10 pin IDE for serial wire debug
5. 3 pin JR battery connector (pin 1 GND, pin 2 VBAT, pin 3 GND)
6. motor connectors (for Racer)
7. connectors for dastardly stuff

## 2.5 Other components

1. We recommend that you use components in the ECE Altium library. These are stocked in the
| SMT lab. For any other components you may require, see Scott Lloyd in the SMT lab.

## 2.6 Reading datasheets

The manufacturer will tell you what they are proud of on the first page. They will omit details of poor aspects.

There is a knack in reading a large datasheet. Here’s what I do first:

1. Look at the example circuits.
2. Read the absolute maximum ratings.
3. Read the pin definitions.

# Chapter 3

# Schematic

## 3.1 Altium tutorial

See the ENCE461 Learn page for the Altium tutorial.

## 3.2 Suggestions

1. If you get the schematic wrong, the PCB will be wrong, and you will have rework grief (see rework).
2. A clear schematic is important for debugging.
3. In general, you should aim to have inputs on the left, outputs on the right, higher voltages at the top.
4. Add notes to explain anything non-obvious.

## 3.3 Check list

You must check the schematic carefully. I use a highlighter to mark every wire and component. If you get the schematic wrong, the PCB will be wrong, and you will have to do much rework, see figure below. And yes, this board worked in the end.

Show photos of rework grief

1. The SPI signals for the radio are connected to the correct MCU pins.
2. The PWM signals for the motor are connected to the correct MCU pins. Note, the PWMLx and PWMHx pins are complementary and cannot be driven independently.
3. All the MCU VDD pins need to be powered.
4. All the MCU GND pins need to be powered.
5. Avoid connecting to PB4 and PB5 (say for TWI1). If you do you will need to disable JTAG in software.

15

16 | CHAPTER 3. SCHEMATIC

# Chapter 4

# PCB layout

Before you lay out your PCB, an hour spent checking your schematic will avoid many hours of testing and rework grief! I annotate a printed schematic with a highlighter to ensure I have considered everything.

## 4.1 Altium tutorial

The Altium tutorial for creating a PCB can be found on the ENCE461 Learn page.

## 4.2 Placement

1. Keep small signal analogue components (radio) well away from digital electronics and power electronics.
2. Place local decoupling capacitors to minimise the loop area.
3. Place bulk capacitors close to where power comes from.
4. Keep the crystal close to the MCU.
5. Place switches so they can be pushed.
6. Place LEDs so they can be seen.
7. Place USB connector so it can be connected to.
8. Place connectors on edge of PCB with wires going away from the board.

## 4.3 Power supplies

1. Use planes for power distribution.
2. If cannot use power plane for power connection, make trace as wide¹ as possible.
3. Do not put splits in planes²

1To reduce inductance and resistance. 2Unless you know what you are doing.

17

18 | CHAPTER 4. PCB LAYOUT
4. Keep planes away from the radio antenna; otherwise the radio range is limited.
5. Before ‘pouring’ a polygon to create a power or ground plane connect the nets with tracks and vias.

## 4.4 Signal traces

1. Use microstrips for any signal above 50 kHz.
2. Keep signal traces apart to reduce crosstalk (3-W rule).
3. Avoid signal traces jumping layers (especially for signals above 50 kHz). If you do, use vias close to ends of traces.
4. Use tented³ vias under components with metal pads.

## 4.5 Recommended layouts

For any switching power supply, sensitive analogue, or BGA fanout, the chip manufacturer usually provides a recommended layout.

## 4.6 Check list

1. Check your schematic. Then get someone else to check your schematic. Query every component.
2. Perform a DRC (Design Rule Check)].
3. Add PCB test points, test points, and more test points. You will need one for every signal
| and power supply. You have been warned! If you don’t believe me, compare the size of an oscilloscope probe to a surface mount IC pin and see if you can hold the probe in place.
4. Label the test points on the silk screen with meaningful names.
5. Add ground test points that you can clip an oscilloscope ground lead to. Keep these away from
| other test points to avoid shorting with the oscilloscope ground clip.
6. Check mounting holes.
7. Check component footprints, especially connectors, voltage regulators, and surface mount
| transistors by placing the parts on a print-out of the PCB design.
8. Ensure that power supply traces are wide as possible, preferably planes, to reduce their inductance.
9. Ensure that high current traces are wide as possible to reduce their resistance.
10. Do not connect IC pins directly between the pads since it is not possible to tell if a solder blob is accidental or deliberate.
11. Insert vias to ground plane to ensure that all parts are connected. Do not leave unconnected copper.

3These have a layer of insulating solder resist.

4.6. CHECK LIST | 19
12. If not using plated through vias do not place vias under components.
13. If placing vias under components with exposed metal pads, make sure the vias are “tented” (covered in solder mask) to prevent unexpected shorts.
14. Stitch power or ground planes where vias or tracks cut them up.
15. If a track is of width W it should be separated from the next track by a width 2W to reduce crosstalk. This is the 3-W rule since the track centres are 3W. An exception is for differential signals; these should be routed close together with a uniform spacing.
16. Do not run a microstrip traces right on the edge of the PCB. If track is of width W it should be at least W from the edge to reduce electric field fringing effects.
17. Use large traces for pads on connectors that may be subject to mechanical forces (power jacks, pluggable terminals, etc.) to prevent trace cracking.
18. If you have high voltages check clearances.
19. Check pad to track clearances to avoid potential solder bridges.
20. Check that it is possible to top-solder through-hole components on non-plated-through boards.
21. Ensure like signals are grouped, data lines, address lines, control lines, analogue signals, etc.
22. Check the thermal path for parts that get hot.
23. Run tracks over reference (power or ground) planes to create a microstrip trace; avoid tracks running over cuts in a reference plane.
24. Check that hole diameters are larger than the pin diameters for connectors and through hole. 25% over the lead diameters is typical. Remember to look at the diagonal dimension for square pins or your holes may be too small.
25. Check the drill file report to make sure the hole sizes are what you would expect. There should be no holes with sizes of zero, no weird sizes, no super large sizes unless required by the design.
26. Check that connections of thermal vias have clearance to other traces and pads.
27. Pay close attention to clearances on internal planes of multilayer boards; shorts on these planes can only be removed with precision drilling.
28. Number pins on connectors, big ICs, selection jumpers, etc. For connectors, number enough pins that pin ordering is obvious. For large ICs consider adding tickmarks every 5 pins.
29. Make the pad for pin 1 of every IC square. Also consider putting a silkscreen dot next to pin 1.
30. Leave at least 20–50 mils (0.5–1.3 mm) clearance between components and the edge of the board. This makes it less likely that inaccuracies in board fabrication will cause part of a pad to get chopped off.
31. Check for component clearances from enclosure including heights.
32. Look at each net individually to ensure that it doesn’t take an overly long path around the board. Many layout tools have a highlight net feature that makes this a fast process.
33. Don’t let the silkscreen overlap pads. Try to avoid having silkscreen overlapping via holes or areas of the board that will be routed away (large holes, slots, tabs, etc.), since legibility will be poor.
34. If ICs are being soldered with solder paste ensure that there is a solder mask between pads.

20 | CHAPTER 4. PCB LAYOUT

## 4.7 Design rule checks

This section considers common Altium design rule violations. For more information see the Altium wiki.

### 4.7.1 PCB manufacture violations

You do not want any of these. If a trace is too thin then etching may produce a hole in it. It two traces are too close together, they may end up joined.

### 4.7.2 PCB assembly violations

SMD neck-down constraint

Traces connecting to SMD pads often need to be reduced in thickness to minimise heat transfer from the SMD pad (unequal PAD temperatures can lead to component tombstoning or rotation in the oven). The traces widths should be a maximum of 50 % of the width of the pad and should be of the same size to prevent component movement due to unequal pad temperatures. The length of the neck-down can be as short as 0.5 mm.

This is not so critical for integrated circuits with many pins (except if a solder mask is not used since solder might flow away from the pad).

Silk to solder mask

Here Altium thinks the silk screen is being printed over a pad; most manufacturers detect this and delete the offending text.

Minimum solder mask sliver constraint

This occurs with chips having pins that are close together. It is a warning that the PCB manufacturer may not be able to make the thin sliver of solder mask that is applied between pads to reduce the chances of having a solder blob between the pins. For a prototype it is not a concern since the solder blob can be easily removed with a small soldering iron.

### 4.7.3 Signal integrity violations

SMD pad to plane constraint

What this means is that you have placed a via to a power or ground plane too far from a SMD pad. Simply add another via closer to the pad. There is no need to skimp on vias for power supply connections.

This violation indicates you that you are adding unnecessary inductance by increasing the loop area and thus compromising signal integrity.

Unfortunately, Altium does not detect when you use a power decoupling capacitor to mitigate this inductance and thus will report false-positives. For some reason, whenever there is a decoupling

4.7. DESIGN RULE CHECKS | 21

capacitor pad between an IC pad and a via to a plane, it cannot calculate the distance of the trace and reports it as being about 2.3 m! So, ignore this error.

The goal is to place the decoupling capacitor to minimise the area of the loop formed by the current flowing from the capacitor to the IC power and ground pins. Multiple vias to power/ground planes should then be placed on the other side of the capacitor.

22 | CHAPTER 4. PCB LAYOUT

# Chapter 5

# PCB assembly

## 5.1 SMT lab induction

You cannot use the SMT lab unless you have performed a lab induction.

## 5.2 Solder pasting

Solder paste needs to be applied to each pad. Usually this is applied using a stencil but for small boards, it can be applied using a syringe. The solder paste must be fresh.

## 5.3 Component placement

The components are placed onto the pasted pads using a pick-and-place machine. The key is to get the orientation of chips, diodes, and LEDs correct.

It is easy to orient the MCU incorrectly. The big dot does not mark pin 1¹

Show image of MCU and where pin 1 is.

## 5.4 Reflow oven

When the board has been populated, the PCB is placed in the reflow oven. At the end of the process, remove your PCB using oven gloves. You do not need to clean the board.

## 5.5 Visual inspection

Look for solder bridges, especially between IC pins. These can be removed with a fine-tipped soldering iron.

Show photo of solder bridge

1
I think they add this to sell more chips.

23

24 | CHAPTER 5. PCB ASSEMBLY

# Chapter 6

# Software installation

Do not underestimate the effort required to flash your first LED. You require:

- A computer with git installed and a useful shell program such as bash. UC has a mirror (http://ucmirror.canterbury.ac.nz/) for a variety of Linux distributions; we recommend Ubuntu or Mint.
- A cloned copy of the Wacky Racers git repository, see project cloning.
- A working ARM toolchain (arm-none-eabi-gcc/g++ version 4.9.3 or newer), see toolchain.
- An ST-link programmer and 10-wire ribbon cable for programming. You can get the adaptor from Scott Lloyd in the SMT lab. You will need to make your own cable (For a grey ribbon cable, align the red stripe with the small arrow denoting pin 1 on the connector. For a rainbow ribbon cable, connect the brown wire to pin 1.). There are two variants of the ST-link programmer with different pinouts so you may need to customise your programming cable.
- Plenty of gumption.

## 6.1 Git

Your group leader should fork the Wacky Racers project template. This creates your own group copy of the project on the eng-git server that you can modify, add members, etc.

Each group member then clones the group project.

### 6.1.1 Project forking

The template software is hosted on the eng-git Git server at https://eng-git.canterbury.ac.nz/wacky-racers/wacky-racers-2021. (https://eng-git.canterbury.ac.nz/wacky-racers/wacky-racers-2021) To fork the template:

1. Go to https://eng-git.canterbury.ac.nz/wacky-racers/wacky-racers-2021.
2. Click the ‘Fork’ button. This will create a copy of the main repository for the project.
3. Click on the ‘Settings’ menu then click the ‘Expand’ button for ‘Sharing and permissions’. Change ‘Project Visibility’ to ‘Private’.
4. Click on the ‘Members’ menu and add group members as Developers.

25

26 | CHAPTER 6. SOFTWARE INSTALLATION

### 6.1.2 Project cloning

Once your project has been forked from the template project, each group member needs to clone it. This makes a local copy of your project on your computer.

If you are using an ECE computer, it is advised that you clone the project on to a removable USB flash drive. This will make git operations and compilation 100 times faster than using the networked file system.

There are two ways to clone the project. If you are impatient and do not mind having to enter a username and password for every git pull and push operation use:

$ git clone
| https://eng-git.canterbury.ac.nz/groupleader-userid/wacky-racers-2021.git
wacky-racers

,→

,→
Otherwise, set up ssh-keys and use:

$ git clone git@eng-git.canterbury.ac.nz:groupleader-userid/wacky-racers-2021.git ,→ wacky-racers

You can have several different cloned copies of your project in different directories. Sometimes if you feel that the world, and git in particular, is against you, clone a new copy, using:

$ git clone
| https://eng-git.canterbury.ac.nz/groupleader-userid/wacky-racers-2021.git
| wacky-racers-new

,→

,→

## 6.2 Toolchain

The toolchain comprises the compiler, linker, debugger, C-libraries, and OpenOCD.

The toolchain is installed on computers in the ESL and CAE. It should run under both Linux and Windows. If there is a problem ask the technical staff.

The toolchain can be downloaded for Windows, Linux, and MacOS from https://developer.arm.com/tools-and-software/open-source-software/developer-tools/gnu-toolchain/gnu-rm/downloads. (https://developer.arm.com/tools-and-software/open-source-software/developer-tools/gnu-toolchain/gnu-rm/downloads)

To install parts of the toolchain separately, see the instructions in the following subsections.

### 6.2.1 Toolchain for Linux

First, if using Ubuntu or Mint, ensure the latest versions are downloaded:

$ sudo apt update && sudo apt upgrade

Then, install the compiler:

$ sudo apt install gcc-arm-none-eabi

Install the C and C++ libraries:

$ sudo apt install libnewlib-arm-none-eabi libstdc++-arm-none-eabi-newlib

Install the debugger, GDB:

$ sudo apt install gdb-multiarch

6.3. IDE | 27

Install OpenOCD:

$ sudo apt install openocd

### 6.2.2 Toolchain for MacOS

For MacOS machines that have homebrew (https://brew.sh) installed, you can use the following command:

$ brew install openocd git
$ brew cask install gcc-arm-embedded

## 6.3 IDE

I am content with using the command-line and emacs as a text editor but I guess that you are not. If you are familiar with geany I suggest that you use that. If you want bells and whistles, I suggest using Visual Studio Code. While it is written by Microsoft, it is free and runs on Windows, Linux and macOS.

### 6.3.1 Visual Studio Code

VS Code is a modern and highly versatile text editor. With the right extensions, it can be used to develop code for just about anything! This project has been configured for VS Code on the ESL computers (but its relatively easy to modify it to work on a home computer, be it Windows, Linux, or Mac). For the simplest use, simply go File -> Open Folder and point it at the wacky-racers repository. This will give you access to the build tools (Ctrl-Shift-B) that have been setup. These must be run from inside a program (i.e., ledflash1.c). Finally, opening a program and pressing F5 will launch a debugging session that will allow the use of breakpoints and variable inspection.

When building your programs, the BOARD configuration variable must be set. In VS Code this is done by choosing your C++ configuration (bottom right of the window) which by default will be either hat or racer.

As a side note, the compilation and debugging requires the installation of two VS Code extensions:

1. C/C++ (Microsoft)
2. Native Debug (Web Freak)

VS Code should automatically prompt you to install these when you open the wacky-racers directory.

28 | CHAPTER 6. SOFTWARE INSTALLATION

# Chapter 7

# First program

Your first program to test your board should only flash an LED (the hello world equivalent for embedded systems). The key to testing new hardware is to have many programs that only do one simple task each.

Before you run your first program, you need to:

1. Install the toolchain.
2. Clone the Wacky Racers git repository, see project cloning.
3. Set up the PIO definitions for your board, see configuration.
4. Compile your program, see compilation.
5. See if your SAM4S is running, see OpenOCD.
6. Configure the SAM4s to boot from flash memory, see booting from flash memory.
7. Program the SAM4s, see programming.

Binary
file
Debugger | OpenOCD | USB
driver | ST-link | SAM4S

PC
Wacky board

Figure 7.1: How OpenOCD interacts with the debugger and the SAM4S.

## 7.1 Connecting with OpenOCD

OpenOCD is used to program the SAM4S, see Figure 7.1.

For this assignment, we use a ST-link programmer to connect to the SAM4S using serial wire debug (SWD). This connects to your board with a 10-wire ribbon cable and an IDC connector.

1. Before you start, disconnect the battery and other cables from your PCB.

29

30 | CHAPTER 7. FIRST PROGRAM
2. Connect a 10-wire ribbon cable from the ST-link programmer to the programming header on
| your PCB. This will provide 3.3 V to your board so your green power LED should light.
3. Open a new terminal window, e.g., bash and start OpenOCD.

$ cd wacky-racers
$ openocd -f src/mat91lib/sam4s/scripts/sam4s_stlink.cfg

All going well, the last line output from OpenOCD should be:

Info : sam4.cpu: hardware has 6 breakpoints, 4 watchpoints

Congrats if you get this! It means you have correctly soldered your SAM4S. If not, do not despair and do not remove your SAM4S. Instead, see troubleshooting.

## 7.2 LED flash program

For your first program, use wacky-racers/src/test-apps/ledflash1/ledflash1.c. (https://eng-git.canterbury.ac.nz/wacky-racers/wacky-racers/-/blob/master/src/test-apps/ledflash1/ledflash1.c) The macros LED1_PIO and LED2_PIO need to be defined in target.h (see configuration).

/* File: ledflash1.c
Author: M. P. Hayes, UCECE
Date: | 15 May 2007
Descr: | Flash an LED
*/
#include <pio.h>

#include "target.h"

#include "pacer.h"

/* Define LED flash rate in Hz. */ #define LED_FLASH_RATE 2

/*
This test app is the faithful blinky program. It works as follows:
1. set the LED pin as an output low (turns on the LED if LED active low).
2. initialize a pacer for 200 Hz.
3. wait for the next pacer tick.
4. toggle the LED.
5. go to step 3.

Suggestions:
* Add more LEDs.
* Blink interesting patterns (S-O-S for example). * Make two LEDs blink at two separate frequencies. */

int
main (void)
{
/* Configure LED PIO as output. */ pio_config_set (LED1_PIO, PIO_OUTPUT_LOW);

7.3. CONFIGURATION | 31

pacer_init (LED_FLASH_RATE * 2);

while (1)
{
/* Wait until next clock tick. */ pacer_wait ();

/* Toggle LED. */
pio_output_toggle (LED1_PIO); }
}

The LED should flash at 2 Hz. If it does not, try the PWM test program and check the frequency with an oscilloscope.

## 7.3 Configuration

Each board has different PIO definitions and requires its own configuration information. The wacky-racers/src/boards (https://eng-git.canterbury.ac.nz/wacky-racers/wacky-racers/-/blob/master/src/boards) directory contains a configuration for the hat and one for the racer board. You must edit these to customise your board. Each configuration directory contains three files:

- board.mk is a makefile fragment that specifies the MCU model, optimisation level, etc.
- target.h is a C header file that defines the PIO pins and clock speeds.
- config.h is a C header file that wraps target.h. Its purpose is for porting to different compilers.

You will need to edit the target.h file for your board and set the definitions appropriate for your hardware. Here’s an excerpt from target.h for a hat board:

/* USB */
#define USB_VBUS_PIO PA5_PIO

/* ADC */
#define ADC_BATTERY PB3_PIO #define ADC_JOYSTICK_X PB2_PIO #define ADC_JOYSTICK_Y PB1_PIO

/* IMU */
#define IMU_INT_PIO PA0_PIO

/* LEDs */
#define LED1_PIO PA20_PIO

#define LED2_PIO PA23_PIO

## 7.4 Compilation

Due to the many files required, compilation is performed using makefiles.

32 | CHAPTER 7. FIRST PROGRAM

The demo test programs are generic and you need to specify which board you are compiling them for. The board configuration file can be chosen dynamically by defining the environment variable BOARD. For example:

$ cd src/test-apps/ledflash1
$ BOARD=racer make

If all goes well, you should see at the end:

text | data | bss | dec | hex filename
11348 | 2416 | 176 | 13940 | 3674 ledflash1.bin

To avoid having to specify the environment variable BOARD, you can define it for the rest of your session using:

$ export BOARD=racer

and then just use:

$ make

## 7.5 Booting from flash memory

By default the SAM4S runs a bootloader program stored in ROM. The SAM4S needs to be configured to run your application from flash memory.

If OpenOCD is running you can do this with:

$ make bootflash

Unless you force a complete erasure of the SAM4S flash memory by connecting the ERASE pin to 3.3 V, you will not need to repeat this command.

## 7.6 Programming

If OpenOCD is running you can store your program in the flash memory of the SAM4S using:

$ make program

When this finishes, one of your LEDs should flash. If so, congrats! If not, see troubleshooting.

To reset your SAM4S, you can use:

$ make reset

## 7.7 Makefiles

Compilation is performed using makefiles, since each application requires many files. Rather than having large makefiles, a heirarchy of makefile fragments is employed. Dependencies are automatically generated (so not all the files have to be recompiled each time).

A board description can be selected with the BOARD environment variable. This can be defined for each command, for example,

7.7. MAKEFILES | 33

$ BOARD=racer make program

Alternatively, this can be defined for a session:

$ export BOARD=racer
$ make program

Each of the makefiles has the following phony targets:

all — compile the application

program — compile the application and download to the MCU (you need Openocd running)

debug — start the debugger GDB (you need Openocd running)

reset — reset the MCU (you need Openocd running)

clean — delete the executable, object files, and dependency files.

34 | CHAPTER 7. FIRST PROGRAM

# Chapter 8

# Test programs

There are a number of test programs in the directory wacky-racers/src/test-apps. (https://eng-git.canterbury.ac.nz/wacky-racers/wacky-racers/-/blob/master/src/test-apps) Where possible these are written to be independent of the target board using configuration files (see configuration).

## 8.1 USB

To help debug your programs, it is useful to be able to print values. This can be achieved by redirecting stdio using the USB CDC protocol. For example, here’s an example program wacky-racers/src/test-apps/usb_serial_test1/usb_serial_test1.c. (https://eng-git.canterbury.ac.nz/wacky-racers/wacky-racers/-/blob/master/src/test-apps/usb_serial_test1/usb_serial_test1.c)

#include <stdio.h>

#include "usb_serial.h"

#include "pio.h"

#include "delay.h"

#define HELLO_DELAY_MS 500

int main (void)
{
int i = 0;

pio_config_set (LED1_PIO, PIO_OUTPUT_LOW);

// Redirect stdio to USB serial usb_serial_stdio_init ();

while (1)
{
delay_ms (HELLO_DELAY_MS);

printf ("Hello world %d\n", i++);

pio_output_toggle(LED1_PIO);
}
}

35

36 | CHAPTER 8. TEST PROGRAMS

To get this program to work you need to compile it and program the SAM4S using:

$ cd wacky-racers/src/test-apps/usb_serial_test1
$ make program

You then need to connect your computer to the USB connector on your PCB. If you are running Linux, run:

$ dmesg

This should say something like:

Apr 30 11:03:50 thing4 kernel: [52704.481352] usb 2-3.3: New USB device found, idVendor=03eb, idProduct=6202
Apr 30 11:03:50 thing4 kernel: [52704.481357] usb 2-3.3: New USB device strings: Mfr=1, Product=2, SerialNumber=3 Apr 30 11:03:50 thing4 kernel: [52704.482060] cdc_acm 2-3.3:1.0: ttyACM0: USB ACM device

Congrats if you see ttyACM0: USB ACM device! If not, see USB debugging. (http://ecewiki.elec.canterbury.ac.nz/mediawiki/index.php/USB_debugging)

You can now run a serial terminal program. (http://ecewiki.elec.canterbury.ac.nz/mediawiki/index.php/Serial_terminal_applications) For example, on Linux:

$ gtkterm -p /dev/ttyACM0

All going well, this will repeatedly print ’Hello world’.

If run Linux and get an error ’device is busy’, it is likely that the ModemManager program has automatically connected to your device on the sly. This program should be disabled on the ECE computers. For more about this and using other operating systems, see USB CDC.

## 8.2 PWM

The program wacky-racers/src/test-apps/pwm_test2/pwm_test2.c (https://eng-git.canterbury.ac.nz/wacky-racers/wacky-racers/-/blob/master/src/test-apps/pwm_test2/pwm_test2.c) provides an example of driving PWM signals.

/* File: pwm_test2.c
Author: M. P. Hayes, UCECE
Date: | 15 April 2013
Descr: | This example starts two channels simultaneously; one inverted
| with respect to the other.
*/
#include "pwm.h"

#include "pio.h"

#define PWM1_PIO PA1_PIO

#define PWM2_PIO PA2_PIO

#define PWM_FREQ_HZ 100e3

static const pwm_cfg_t pwm1_cfg =
{
.pio = PWM1_PIO,
.period = PWM_PERIOD_DIVISOR (PWM_FREQ_HZ), .duty = PWM_DUTY_DIVISOR (PWM_FREQ_HZ, 50),

8.2. PWM | 37

.align = PWM_ALIGN_LEFT,
.polarity = PWM_POLARITY_LOW, .stop_state = PIO_OUTPUT_LOW };

static const pwm_cfg_t pwm2_cfg =
{
.pio = PWM2_PIO,
.period = PWM_PERIOD_DIVISOR (PWM_FREQ_HZ), .duty = PWM_DUTY_DIVISOR (PWM_FREQ_HZ, 50), .align = PWM_ALIGN_LEFT,
.polarity = PWM_POLARITY_HIGH,
.stop_state = PIO_OUTPUT_LOW
};

int
main (void)
{
pwm_t pwm1;
pwm_t pwm2;

pwm1 = pwm_init (&pwm1_cfg);
pwm2 = pwm_init (&pwm2_cfg);
pwm_channels_start (pwm_channel_mask (pwm1) | pwm_channel_mask (pwm2));

while (1)
continue;

return 0;
}

Notes:

1. This is for a different H-bridge module that requires two PWM signals and forward/reverse signals. You will need to generate four PWM signals or be clever with two PWM signals.
2. The pwm_cfg_t structure configures the frequency, duty cycle and alignment of the output PWM.
3. The frequency is likely to be too high for your motor.
4. pwm_channels_start is used to start the PWM channels simultaneously.

The most likely problem is that you have not used a PIO pin that can be driven as a
PWM output. | The SAM4S can generate four independent hardware PWM signals. | See
wacky-racers/src/mat91lib/pwm/pwm.c (https://eng-git.canterbury.ac.nz/wacky-racers/wacky-racers/-/blob/master/src/mat91lib/pwm/pwm.c) for a list of supported PIO pins. Note, PA16, PA30, and PB13 are different options for PWM2.

To drive the motors you will need to use a bench power supply. Start with the current limit set at 100 mA maximum in case there are any board shorts. When all is well, you can increase the current limit; you will need at least 1 A.

38 | CHAPTER 8. TEST PROGRAMS

## 8.3 IMU

The MPU9250 IMU connects to the SAM4S using the I2C bus (aka TWI bus). The program wacky-racers/src/test-apps/imu_test1/imu_test1.c (https://eng-git.canterbury.ac.nz/wacky-racers/wacky-racers/-/blob/master/src/test-apps/imu_test1/imu_test1.c) provides an example of using the MPU9250 IMU. All going well, this prints three 16-bit acceleration values per line to USB CDC. Tip your board over, and the the third (z-axis) value should go negative since this measures the effect of gravity on a little mass inside the IMU pulling on a spring.

If you get ‘ERROR: can’t find MPU9250!’, the main reasons are:

1. You have specified the incorrect address. Use 0x68 for MPU_ADDRESS in target.h if the AD0 pin is connected to ground otherwise use 0x69.
2. You are using TWI1. The PB4 and PB5 pins used by TWI1 default to JTAG pins. See disabling JTAG pins.

See also IMU checking.

Other problems:

1. If you reset the SAM4S in the middle of a transaction with the IMU, the IMU gets confused and
| holds the TWD/SDA line low. This requires recycling of the power or sending out some dummy
clocks on the TWCK/SCL signal.

## 8.4 Radio

The program wacky-racers/src/test-apps/radio_tx_test1/radio_tx_test1.c (https://eng-git.canterbury.ac.nz/wacky-racers/wacky-racers/-/blob/master/src/test-apps/radio_tx_test1/radio_tx_test1.c) provides an example of using the radio as a transmitter.

The companion program wacky-racers/src/test-apps/radio_rx_test1/radio_rx_test1.c (https://eng-git.canterbury.ac.nz/wacky-racers/wacky-racers/-/blob/master/src/test-apps/radio_rx_test1/radio_rx_test1.c) provides an example of using the radio as a receiver.

/* File: radio_rx_test1.c
Author: M. P. Hayes, UCECE
Date: 24 Feb 2018
*/
#include "nrf24.h"

#include "usb_serial.h"

#include "pio.h"

#include "delay.h"

#define RADIO_CHANNEL 4

#define RADIO_ADDRESS 0x0123456789LL

static void panic (void)
{
while(1)
{
pio_output_toggle (LED1_PIO); pio_output_toggle (LED2_PIO); delay_ms (400);
}

8.4. RADIO | 39

}

int main(void)
{
nrf24_cfg_t nrf24_cfg =
{
.channel = RADIO_CHANNEL,
.address = RADIO_ADDRESS,
.payload_size = 32,
.ce_pio = RADIO_CE_PIO,
.irq_pio = RADIO_IRQ_PIO,
.spi =
{
.channel = 0,
.clock_speed_kHz = 1000,
.cs = RADIO_CS_PIO,
.mode = SPI_MODE_0,
.cs_mode = SPI_CS_MODE_FRAME, .bits = 8
}
};
nrf24_t *nrf;

// Configure LED PIO as output. pio_config_set (LED1_PIO, PIO_OUTPUT_LOW); pio_config_set (LED2_PIO, PIO_OUTPUT_HIGH);

// Redirect stdio to USB serial. usb_serial_stdio_init ();

#ifdef RADIO_PWR_EN

// Enable radio regulator if present. pio_config_set (RADIO_PWR_EN, PIO_OUTPUT_HIGH); delay_ms (10);
#endif

nrf = nrf24_init (&nrf24_cfg); if (! nrf)
panic ();

while(1)
{
char buffer[33];
uint8_t bytes;

bytes = nrf24_read (nrf, buffer, sizeof (buffer)); if (bytes != 0)
{
buffer[bytes] = 0;
printf ("%s\n", buffer);

40 | CHAPTER 8. TEST PROGRAMS

pio_output_toggle (LED1_PIO); }
}
}

Notes:

1. Both programs must use the same RF channel and the same address.
2. Some RF channels are better than others since some overlap with WiFi and Bluetooth.
3. The address is used to distinguish devices operating on the same channel. Note, the transmitter
| expects an acknowledge from a receiver on the same address and channel.
4. The number of bytes that can be transmitted is set by the payload\size field in the configuration structure. This has a maximum value of 32.
5. The radio ‘write‘ method blocks waiting for an auto-acknowledgement from the receiver device.
| This acknowledgement is performed in hardware. If no acknowledgement is received, it retries for up to 15 times. The auto-acknowledgement and number of retries can be configured in

software.

6. If the program hangs in the panic loop, there is no response from the radio module, check SPI connections and see SPI debugging.
7. The radio has two modes: transmit and receive. Calling nrf24_write switches to transmit mode and calling nrf24_read switches to receive mode.

If you cannot communicate between your hat and racer boards, try communicating with the radio test modules Scott Lloyd has in the SMT lab.

## 8.5 ADC

wacky-racers/src/test-apps/adc_usb_serial_test2/adc_usb_serial_test2.c (https://eng-git.canterbury.ac.nz/wacky-racers/wacky-racers/-/blob/master/src/test-apps/adc_usb_serial_test2/adc_usb_serial_test2.c) shows how to read from two multiplexed ADC channels. For more details see wacky-racers/src/mat91lib/adc/adc.h. (https://eng-git.canterbury.ac.nz/wacky-racers/wacky-racers/-/blob/master/src/mat91lib/adc/adc.h)

/* File: adc_usb_serial_test2.c
Author: M. P. Hayes, UCECE
Date: | 3 May 2021
Descr: | This reads from ADC channels 2 and 4.
| It triggers ADC conversions as each sample is read.
*/
#include <stdio.h>

#include "usb_serial.h"

#include "adc.h"

#include "pacer.h"

#define PACER_RATE 2

static const adc_cfg_t adc_cfg =
{
.bits = 12,
.channels = BIT (ADC_CHANNEL_2) | BIT (ADC_CHANNEL_4),
.trigger = ADC_TRIGGER_SW,

8.6. PUSHBUTTON | 41

.clock_speed_kHz = 1000
};

int main (void)
{
usb_cdc_t usb_cdc;
adc_t adc;
int count = 0;

// Redirect stdio to USB serial usb_serial_stdio_init ();

adc = adc_init (&adc_cfg);

pacer_init (PACER_RATE);
while (1)
{
uint16_t data[2];

pacer_wait ();

// The lowest numbered channel is read first. adc_read (adc, data, sizeof (data));

printf ("%3d: %d, %d\n", count, data[0], data[1]); }
}

The ADC can be also set up to stream data continuously but you need to use interrrupts or DMA.

## 8.6 Pushbutton

wacky-racers/src/test-apps/button_test1/button_test1.c (https://eng-git.canterbury.ac.nz/wacky-racers/wacky-racers/-/blob/master/src/test-apps/button_test1/button_test1.c) shows the use of a simple button driver to read a pushbutton. This driver does not debounce the button.

/* File: button_test1.c
Author: M. P. Hayes, UCECE
Date: | 18 Dec 2021
Descr: | Simple button test demo without debouncing
*/
#include "mcu.h"

#include "pio.h"

#include "pacer.h"

#define PACER_RATE 100

int
main (void)
{

42 | CHAPTER 8. TEST PROGRAMS
/* Configure LED PIO as output. | */
pio_config_set (LED1_PIO, PIO_OUTPUT_LOW);

/* Configure button PIO as input with pullup. */ pio_config_set (BUTTON_PIO, PIO_INPUT_PULLUP);

pacer_init (PACER_RATE);

while (1)
{
/* Wait until next clock tick. */ pacer_wait ();

if (pio_input_get (BUTTON_PIO)) pio_output_high (LED1_PIO); else
pio_output_low (LED1_PIO); }
}

wacky-racers/src/test-apps/button_test2/button_test2.c (https://eng-git.canterbury.ac.nz/wacky-racers/wacky-racers/-/blob/master/src/test-apps/button_test2/button_test2.c) shows the use of a simple button driver to read a pushbutton. This driver does button debouncing and state-transition detection. For more details see wacky-racers/src/mmculib/button/button.h. (https://eng-git.canterbury.ac.nz/wacky-racers/wacky-racers/-/blob/master/src/mmculib/button/button.h)

/* File: button_test2.c
Author: M. P. Hayes, UCECE
Date: | 3 May 2021
Descr: | Simple button test demo using debouncing
*/
#include "mcu.h"

#include "led.h"

#include "pio.h"

#include "pacer.h"

#include "button.h"

#define BUTTON_POLL_RATE 100

/* Define LED configuration. */ static const led_cfg_t led1_cfg = {
.pio = LED1_PIO,
.active = 1
};

/* Define button configuration. */ static const button_cfg_t button1_cfg = {
.pio = BUTTON_PIO
};

8.7. LEDTAPE | 43

int main (void)
{
led_t led1;
button_t button1;

/* Initialise LED. */
led1 = led_init (&led1_cfg);

/* Turn on LED. */
led_set (led1, 1);

/* Initialise button. */
button1 = button_init (&button1_cfg);

button_poll_count_set (BUTTON_POLL_COUNT (BUTTON_POLL_RATE));

pacer_init (BUTTON_POLL_RATE);

while (1)
{
pacer_wait ();

button_poll (button1);

if (button_pushed_p (button1)) {
led_toggle (led1);
}
}
return 0;
}

## 8.7 LEDtape

wacky-racers/src/test-apps/ledtape_test1/ledtape_test1.c (https://eng-git.canterbury.ac.nz/wacky-racers/wacky-racers/-/blob/master/src/test-apps/ledtape_test1/ledtape_test1.c) shows how to drive the LEDtape.

/* File: ledtape_test11.c
Author: M. P. Hayes, UCECE
Date: | 30 Jan 2020
Descr: | Test ledtape
*/

#include <pio.h>

#include "target.h"

#include "pacer.h"

#include "ledtape.h"

#define NUM_LEDS 20

44 | CHAPTER 8. TEST PROGRAMS

/*
| This test app shows how to program the WS2318B LED tape. In this example the ledtape_write() function is used to send the appropriate GRB color information down the LED tape. It takes care of all the tricky timings, you just need to feed it an array of color values.

ledtape_write(
| pin - This is the pin you want to send the data on. Should be connected
to your level shifter.
| data - This is the array of GRB data (8 bit values, 24 bits per pixel). size - This is the size of the array in bytes.

)

| You will also see use of the pacer module. This isn't really needed, but makes it easier to see the data packets being sent if you put the data

signal on an oscilloscope.

Suggestions:
| * Change the number of LEDs to match yours (or move the NUM_LEDS definition
to your target file)
* Change the color being set on all the LEDs.
* Make an interesting pattern.
| * Make the pattern scroll down the LEDs (see ledtape_test2 for an option).
*/

int
main (void)
{
uint8_t leds[NUM_LEDS * 3]; int i;

for (i = 0; i < NUM_LEDS; i++) {
// Set full green GRB order leds[i * 3] = 255;
leds[i * 3 + 1] = 0;
leds[i * 3 + 2] = 0;
}

pacer_init(10);

while (1)
{
pacer_wait();

ledtape_write (LEDTAPE_PIO, leds, NUM_LEDS * 3); }
}

8.7. LEDTAPE | 45

wacky-racers/src/test-apps/ledtape_test2/ledtape_test2.c (https://eng-git.canterbury.ac.nz/wacky-racers/wacky-racers/-/blob/master/src/test-apps/ledtape_test2/ledtape_test2.c) uses a more sophisticated means of controlling the LEDs.

/* File: ledtape_test2.c
Author: B Mitchell, UCECE
Date: | 14 April 2021
Descr: | Test ledtape
*/

#include <pio.h>

#include "target.h"

#include "pacer.h"

#include "ledbuffer.h"

#define NUM_LEDS 15

/*
This is an alternative method for driving the LED tape using the ledbuffer module that is included in the ledtape driver.

The buffer acts like a small framebuffer upon which you can set RGB values at specific positions (not GRB, it handles the translation automatically). It also makes it easy to make patterns, shuffle them allow the strip, and clear it later. See ledbuffer.h for more details (CTRL-Click it in VS Code). */

int
main (void)
{
bool blue = false;
int count = 0;

ledbuffer_t* leds = ledbuffer_init(LEDTAPE_PIO, NUM_LEDS);

pacer_init(30);

while (1)
{
pacer_wait();

if (count++ == NUM_LEDS)
{
// wait for a revolution
ledbuffer_clear(leds);
if (blue)
{
ledbuffer_set(leds, 0, 0, 0, 255); ledbuffer_set(leds, NUM_LEDS / 2, 0, 0, 255); }
else

46 | CHAPTER 8. TEST PROGRAMS

{
ledbuffer_set(leds, 0, 255, 0, 0);
| ledbuffer_set(leds, NUM_LEDS / 2, 255, 0, 0);
}
blue = !blue;
count = 0;
}

ledbuffer_write (leds);
ledbuffer_advance (leds, 1); }
}

# Chapter 9

# Application

Here are my recommendations for your Hat or Racer application:

1. Build and test your programs incrementally.
2. Write separate test programs that you can run when your application fails to work. When debugging embedded systems, it is much easier to use a small test program rather than a large application.
3. It is easier to use a paced loop and poll the peripherals than using interrupts.
4. Disable the watchdog timer until you have robust code.

47

48 | CHAPTER 9. APPLICATION

# Chapter 10

# Libraries

mmculib is a library of C drivers, mostly for performing high-level I/O. It is written to be microcontroller neutral.

mat91lib is a library of C drivers specifically for interfacing with the peripherals of Atmel AT91 microcontrollers such as the Atmel SAM4S. It provides the hardware abstraction layer.

If you find a bug or would like additional functionality let us know.

## 10.1 PIO pins

mat91lib provides efficient PIO abstraction routines in wacky-racers/src/mat91lib/sam4s/pio.h. (https://eng-git.canterbury.ac.nz/wacky-racers/wacky-racers/-/blob/master/src/mat91lib/sam4s/pio.h) Each pin can be configured as follows:

PIO_INPUT, | /* Configure as input pin. | */
PIO_PULLUP, | /* Configure as input pin with pullup. | */
PIO_PULLDOWN, | /* Configure as input pin with pulldown. | */
PIO_OUTPUT_LOW, | /* Configure as output, initially low. | */
PIO_OUTPUT_HIGH, | /* Configure as output, initially high. | */
PIO_PERIPH_A, | /* Configure as peripheral A. | */
PIO_PERIPH_A_PULLUP, | /* Configure as peripheral A with pullup. | */
PIO_PERIPH_B, | /* Configure as peripheral B. | */
PIO_PERIPH_B_PULLUP, | /* Configure as peripheral B with pullup. | */
PIO_PERIPH_C, | /* Configure as peripheral C. | */
PIO_PERIPH_C_PULLUP | /* Configure as peripheral C with pullup. | */

Here’s an example:

#include "pio.h"

// Configure PA0 as an output and set default state to low. pio_config_set (PIO_PA0, PIO_OUTPUT_LOW);

// Set PA0 high.
pio_output_high (PIO_PA0);

// Set PA0 low.

49

50 | CHAPTER 10. LIBRARIES

pio_output_low (PIO_PA0);

// Set PA0 to value.
pio_output_set (PIO_PA0, value);

// Toggle PA0.
pio_output_toggle (PIO_PA0);
| // Reonfigure PA0 as an output connected to peripheral A.
pio_config_set (PIO_PA0, PIO_PERIPH_A);

// Reonfigure PA0 as an input with pullup enabled. pio_config_set (PIO_PA0, PIO_INPUT_PULLUP);

// Read state of PIO pin.
result = pio_input_get (PIO_PA0);

Note, you can reconfigure a PIO pin on the fly. For example, you may want the pin to be driven by the PWM peripheral and then at some stage forced low. To do this, use pwm\_config\_set.

## 10.2 Delaying

mat91lib provides a macro DELAY_US in wacky-racers/src/mat91lib/delay.h (https://eng-git.canterbury.ac.nz/wacky-racers/wacky-racers/-/blob/master/src/mat91lib/delay.h) for a busy-wait delay in microseconds (this can be a floating point value). The CPU busy-waits for a precomputed number of clock cycles. The argument should be a constant so the compiler can compute the number of clock cycles.

mat91lib also provides a function delay_ms for a busy-wait delay in milliseconds (this must be an integer). All this function does is call DELAY_US (1000) the required number of times.

An example program is wacky-racers/src/test-apps/delay_test1/delay_test1.c. (https://eng-git.canterbury.ac.nz/wacky-racers/wacky-racers/-/blob/master/src/test-apps/delay_test1/delay_test1.c)

## 10.3 Miscellaneous

### 10.3.1 Disabling JTAG pins

By default PB4 and PB5 are configured as JTAG pins. You can turn them into PIO pins or use them for TWI1 using:

#include "mcu.h"

void main (void)
{
mcu_jtag_disable ();
}

10.4. I/O MODEL | 51

### 10.3.2 Watchdog timer

The watchdog timer is useful for resetting the SAM4S if it hangs in a loop. It is disabled by default but can be enabled using:

#include "mcu.h"

void main (void)
{
mcu_watchdog_enable ();

while (1)
{
/* Do your stuff here. */

mcu_watchdog_reset ();
}
}

## 10.4 I/O model

The mat91lib and mmculib libraries try to use the POSIX I/O model. In general, non-blocking I/O is used so if data is not available, the functions return without waiting, or with a short timeout.

The read/write functions have three arguments:

1. A device handle created by the init function.
2. A pointer to a buffer.
3. The number of bytes to transfer (type size_t)

The return value is of type ssize_t and is either:

1. The number of bytes transferred if greater than or equal to zero.
2. -1 for error, in which case the error number is stored in errno.

Here is an example:

char *buffer[4];

ret = adc_read (adc, buffer, sizeof (buffer));

## 10.5 Coding style

For the curious, the GNU C coding style is used. I worked as a compiler engineer for the USA company Cygnus Solutions (taken over by Redhat) on the GNU C compiler (GCC). The first-rule when working as a programmer for a company is to follow the required coding style. My text editor (emacs) is set up to default to this style.

52 | CHAPTER 10. LIBRARIES

## 10.6 Under the bonnet

The building is controlled by wacky-racers/src/mat91lib/mat91lib.mk. (https://eng-git.canterbury.ac.nz/wacky-racers/wacky-racers/-/blob/master/src/mat91lib/mat91lib.mk) This is a makefile fragment loaded by wacky-racers/src/mmculib/mmculib.mk. (https://eng-git.canterbury.ac.nz/wacky-racers/wacky-racers/-/blob/master/src/mmculib/mmculib.mk) wacky-reacers/src/mat91lib/mat91lib.mk loads other makefile fragments for each peripheral or driver required. It also automatically generates dependency files for the gazillions of other files that are required to make things work.

# Chapter 11

# Troubleshooting

Troubleshooting can be frustrating when you are tired. You need plenty of gumption and an open mind. Difficult problems are usually a combination of two or more problems. So do not attempt if you are tired or in a hurry.

Before you start, you need an A3 printed schmematic, annotated with any changes your group may have made.

## 11.1 The scientific method

Successful troubleshooting requires application of the scientific method. First you form a hypothesis about the cause of the problem and then you test your hypothesis by making observations. If the observations do not confirm your hypothesis, you need to revise your hypothesis and make more observations.

For example, let’s say the IMU does not work. A hypothesis is that the chip has no power, so you test this by measuring the power supply voltage at the chip with an oscilloscope. But why not use a multimeter? Well, a multimeter only gives the average value and will not show you that a voltage regulator is oscillating or if there is a lot of noise. If the power supply looks fine, you need another hypothesis, say that the MCU is not outputting I2C signals. You then make observations of the I2C signals, with an oscilloscope, to see if they are changing. If the waveforms seem fine, you might hypothesise that the IMU is not configured for the correct I2C address. So you then check that the acknowledge bit is driven low by the IMU. If there is no acknowledgement, you then check the address that the IMU is configured for and the address sent over the I2C bus. If these match, you might hypothesise that there is a poor electrical connection. So you look at the soldering under a microscope, and so forth.

When forming hypotheses, you need to start with the more likely ones. Hypothesising that a chip is blown is unlikely unless you observed the release of magic smoke, noticed that the chip got very hot, noticed an electrostatic spark, or applied a high voltage, say by putting your PCB on something conductive.

As you get more desperate, you need more outlandish hypotheses about what may have gone wrong. Here, experience helps. However, the key is forming a hypothesis based on previous observations¹ .

1
“Once you eliminate the impossible, whatever remains, no matter how improbable, must be the truth.” — Sherlock Homes.

53

54 | CHAPTER 11. TROUBLESHOOTING

## 11.2 Oscilloscope

The best tool for debugging an embedded system is an oscilloscope.

1. Use ×10 probes to reduce loading on the circuit.
2. Use the correct probes for the scope so that they can be automatically detected.
3. Compensate the probes by clipping to the probe test signal on the scope and adjusting the
| variable capacitor in the probe to ensure a square wave without undershoot or overshoot. This is one of the few times you are allowed to use the autoscale button!
4. Check that the probe gains are correct; they should by ×10 for ×10 probes.
5. Hypothesise what you should expect to observe and set up the oscilloscope accordingly. Pushing
| the auto-set button only works for AC or DC signals and is hopeless for transient signals, such as I2C bus waveforms. For transient signals, use normal mode triggering.

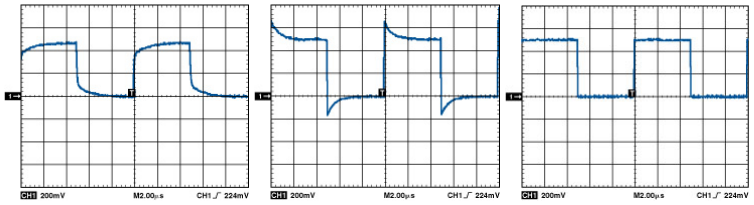
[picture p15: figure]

Figure 11.1: Oscilloscope probe compensation: under, over, and proper. From http://www.analog.com/library/analogdialogue/archives/41-03/time domain.html. (http://www.analog.com/library/analogdialogue/archives/41-03/time_domain.html)

### 11.2.1 Normal mode

This mode is for measuring transient or non-repetitive signals, such a serial bus waveforms. It will only refresh the display if a trigger event is detected. You need to adjust the trigger level.

It is useful to increase the trigger holdoff to prevent triggering on multiple edges of a waveform. By default, it is set to a ridiculously small value.

### 11.2.2 Auto mode

This mode is for measuring AC or DC signals. It is like normal mode but if it does not detect a trigger it will automatically refresh the display.

## 11.3 SAM4S not detected by OpenOCD

If a program has not been loaded:

1. Check orientation of the SAM4S (the large circle does not mark pin 1).
2. Check soldering of the SAM4S pins under a microscope. Giving each pin a push with a sharp spike can reveal a poorly soldered joint.

11.3. SAM4S NOT DETECTED BY OPENOCD | 55
3. Check 3.3 V and 1.2 V power rails.
4. Check the serial wire debug (SWD) signals, see debugging serial wire debug (SWD).

If a program has been loaded:

1. Check the crystal oscillator.
2. Erase flash memory.
3. Re-enable booting from flash memory.
4. Reprogram the SAM4S with an LED flash program.

### 11.3.1 Erasing flash memory

1. Connect the ERASE pin to 3.3 V.
2. Re-start OpenOCD.
3. Re-enable booting from flash memory.

### 11.3.2 Debugging serial wire debug (SWD)

OpenOCD periodically polls to see if the SAM4S is alive. These occur every 100 ms, see Figure 11.2. If the SAM4S responds, the waveform seen in Figure 11.3 should be observed on the SWD pin.

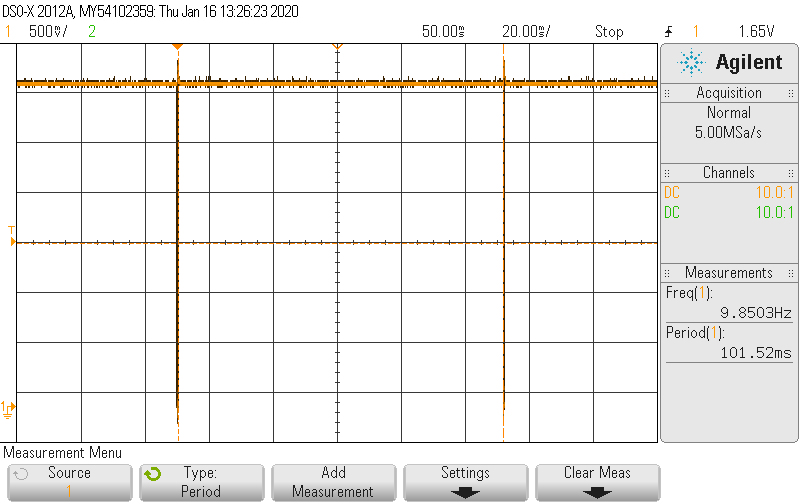
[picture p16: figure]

Figure 11.2: OpenOCD polls every 100 ms while connected.

OpenOCD polls less often when it does not get a response. The period increases to 6.3 s.

### 11.3.3 Checking the crystal oscillator

When the SAM4S is first powered up it uses an internal RC oscillator. However, when a program is loaded, the code before main is called switches the SAM4S to use the main oscillator that uses the external crystal. If there is a problem with the crystal oscillator the SAM4S will not run since it has no clock. Moreover, OpenOCD will then fail to communicate with the SAM4S.

56 | CHAPTER 11. TROUBLESHOOTING

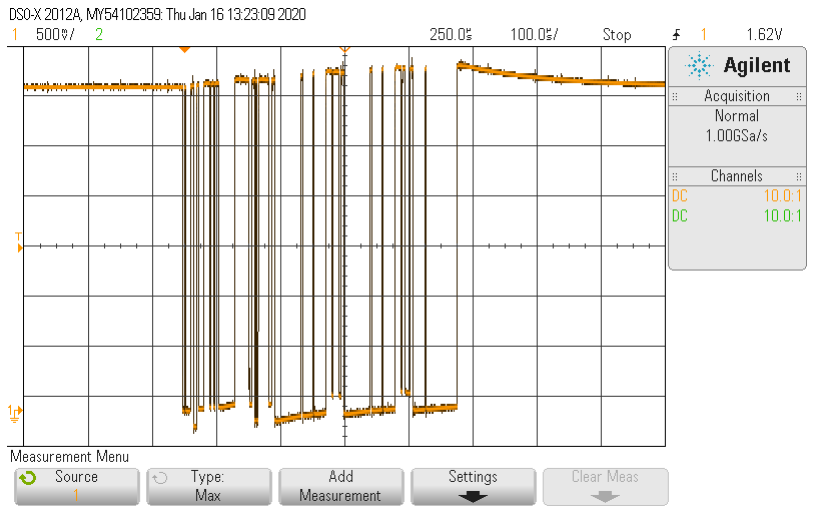
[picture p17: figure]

Figure 11.3: SWD signal when there is a response from the SAM4S.

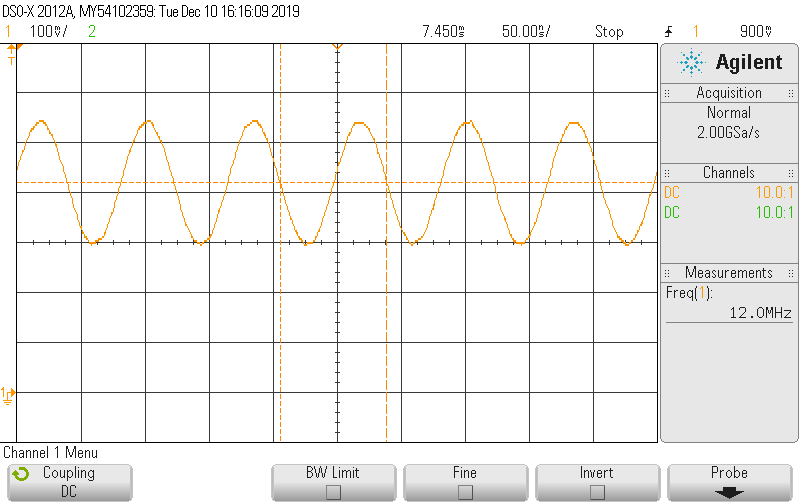
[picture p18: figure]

Figure 11.4: 12 MHz clock sine wave measured on the XOUT pin.

Add scope picture of CPU clock signals when not working

Figure 11.5: Oscillator waveform when not working.

1. Connect a scope pin to the XOUT pin. A 12 MHz sinewave should be visible, see Figure 11.4.
2. If there is no sinewave:
(a) Measure the voltage on the VDDPLL pin of the MCU with a scope. This should be 3.3 V to power the oscillator.
(b) Check the bypass capacitors across the crystal. These should be approx. 20 pF.

### 11.3.4 Checking the clock

The SAM4s has multiple clock sources:

11.4. USB SERIAL | 57
1. Internal fast RC oscillator (this is selected when the SAM4S is first ever used).
2. Internal slow RC oscillator (this can be selected to save power).
3. Main oscillator using external crystal.

The SAM4S uses a phase-locked-loop (PLL) to multiply the frequency of the clock source to provide the CPU clock. Sometimes the PLL will run without a clock source and thus will generate an unexpected frequency.

The clock frequency can be checked by connecting a scope to a peripheral pin that generates a clock, e.g., PWM, SCK, TXD, and programming the peripheral.

## 11.4 USB serial

USB is a complicated protocol and there are many possibilities why it does not work.

- Check that the termination resistors are 27 ohms.
- Check the SAM4S is running at the correct frequency of 96 MHz² | . Check the SAM4S XIN
pin with an oscilloscope for a 12 MHz sinusoid. Note, the oscillator is not enabled unless a program has been loaded and running. If a 12 MHz signal is not found, check the MCU solder connections under a microscope. Also check that the VDDPLL pin has 3.3 V.

If the USB serial connection drops characters:

- Add a delay before sending data. This is because the driver takes a while to set up the connection after the USB cable is plugged in. If you try to send some data during this time, the data gets stored into a ring buffer for later transmission. However, the ring buffer is not large and once it is filled, the USB serial driver will drop characters.

## 11.5 Motors

For the motors to work:

1. The H-bridge must be correctly configured.
2. The PWM signals must be correctly generated.

### 11.5.1 Testing the H-bridge

1. The nFAULT pin should be high. Note, this is an open-drain pin and requires a pullup resistor to 3V3 to make it work. Without this resistor, this pin will always read low, fault or no fault. If this is connected to the SAM4S, it will be pulled up by default.
2. The nSLEEP pin needs to be high to enable the chip.
3. Check that the capacitor connected to the INT pin is 2.2 µF and not 2.2 nF.
4. Check the AIN1, AIN2, BIN1, BIN2 pins. If you see DC 2 V, this is due to the signal not being configured as an output on the SAM4S; the internal pullup of the SAM4S forms a voltage divider with the internal pulldown of the H-bridge chip.

2The SAM4S has two PLLs so it is possible to clock the CPU at other frequencies.

58 | CHAPTER 11. TROUBLESHOOTING
5. Check that AINSENSE and BINSENSE are connected directly to ground or to ground via a small resistor if you want current limiting.

### 11.5.2 Debugging PWM

If PWM does not work:

1. Check the SAM4S pin since not every pin can be a PWM signal.
2. Check the definition in the configuration file target.h

If the PWM frequency is wrong:

1. Check the clock frequency, see checking the clock.
2. Check your program.

If the PWM duty is wrong:

1. Check your program. The duty is specified as an integer in parts per thousand. (e.g., 1000 = 100% duty cycle; 50 = 5% duty cycle)

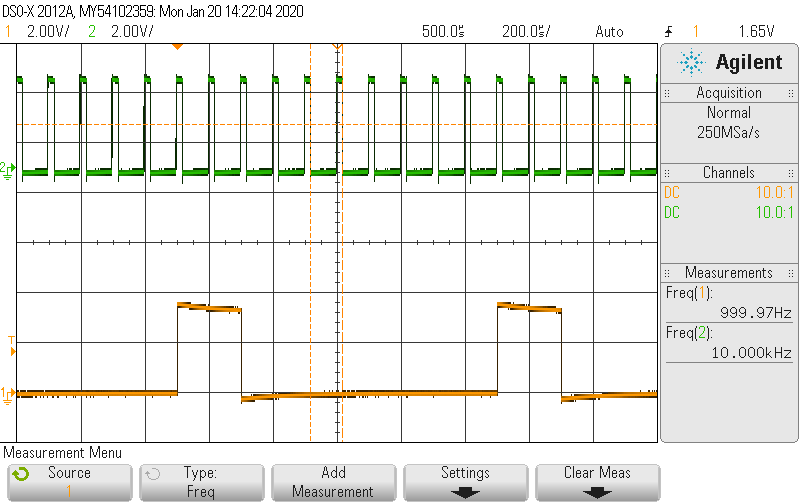
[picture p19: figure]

Figure 11.6: Two PWM signals at 1 kHz and 10 kHz.

## 11.6 IMU

For the IMU to work:

1. The IMU chip must be correctly configured.
2. The I2C bus must be working.

### 11.6.1 IMU checking

1. Check the I2C bus (see debugging I2C).
2. Check the auxiliary I2C bus signals are not connected on the IMU (otherwise the magnetometer will not respond).

11.7. NRF24L01+ RADIO | 59
3. Check nCS on the IMU is pulled high.
4. Check FSYNC on the IMU is pulled low.
5. Try pressing on a side of the IMU with a fingernail to see if it starts working; you might have a dry joint. Otherwise look under the microscope at the pins of the IMU and touch them up with a soldering iron if necessary.

### 11.6.2 Debugging I2C

1. I2C/TWI requires external pull-up resistors for the clock (TCK) and data (TDA) signals. Use a scope to look at the signals TWCK/SCL and TWD/SDA. If the rise times are too slow so that the high voltage level is not 3.3 V, the resistors are too large.
2. TWI channel 1 (TWI1) uses PB4 and PB5. However, these are configured on boot as JTAG pins. You can disable this, see disabling JTAG pins.

Add scope picture of I2C signals

Figure 11.7: I2c signals with acknowledgement.

Add scope picture of I2C signals with no acknowledge

Figure 11.8: I2c signals with no acknowledgement.

## 11.7 NRF24L01+ radio

For the radio to work you need:

1. No ground planes near the antenna³ .
2. A working SPI interface.
3. The correct channel and address.
4. A well filtered power supply for the radio, see Figure 2.1.
5. A channel with little interference (note, some channels are shared with WiFi and Bluetooth and may be less reliable).

If nothing works, check:

1. For transmission the CE pin should be low; for reception the CE pin should be high.
2. Check that the SPI clock SCK, MOSI, and MISO signals are driven when the radio is configured (note, the MISO signal is tristate when CS is high).
3. Check that the SPI CS signal is driven low for each transmitted byte.

If the radio transmits but not receives, check:

1. The IRQ pin is driven low (this indicates that a packet has been received).

3You might have to mount the radio vertically.

60 | CHAPTER 11. TROUBLESHOOTING
2. The power supply. The radio requires a well filtered power supply otherwise the range will be
| limited on reception. Preferably, the device should have its own 3V3 regulator with a low-pass RC filter comprised of a series resistor and large capacitor (say 22 µF) or a low-pass LC filter

made with a ferrite bead and capacitor.

Note, by default the radio waits for an auto-acknowledgement from the receiver device. This acknowledgement is performed in hardware. If no acknowledgement is received, it retries for up to 15 times. The auto-acknowledgement and number of retries can be configured in software.

### 11.7.1 Checking the radio power supply

Add scope picture of expected radio power supply voltage

Figure 11.9: Waveform showing radio power supply voltage.

### 11.7.2 Debugging SPI

Check:

1. The device chip select signal is driven low.
2. The SCK signal toggles while the chip select is low.
3. The MOSI signal does something while the chip select is low.

The MISO signal is usually tri-state and is driven by the device when the chip select is low.

The SPI standard is rather loose and there are four modes to confuse the unwary; these are due to two clock polarity modes and two clock phase modes. When using the wrong mode, the read data can be out by a bit or unreliable.

Add scope picture of SPI signals

Figure 11.10: SPI signals.

## 11.8 Other problems

1. OpenOCD does not run. The most common problem is that the USB permissions are not correct⁴ .
2. A program does not correctly build after a file has been changed. Every now and then the file timestamps are incorrect (this is a common problem with network drives due to a skew in the clocks) and make will not correctly rebuild a file. Running make clean will remove the existing dependency and object files so you can start afresh.
3. A program hangs. This can be observed by an LED no longer flashing. There are a number of reasons:
(a) The program is stuck in an infinite loop. Note, an embedded system should only have an infinite loop for the main loop; all other loops should have a timeout condition.

4On Linux this is controlled by udev.

11.8. OTHER PROBLEMS | 61
(b) The program has crashed trying to access invalid memory. Usually this is due to buffer overflow or dereferencing uninitialised pointers (say by not calling radio_init). Try running make debug. This will start the debugger and attach to your MCU. If the debugger says that your program has stopped in _hardfault_handler, then your program is likely to have accessed invalid memory. Use the bt command to print a stack trace to see how your program went astray.
(c) You are printing output using USB but a terminal program is not running.
4. The output of the 3V3 regulator works fine when powered from USB but gives 6 V when powered from a 7.2 V battery. Check that the 7.2 V is not connected directly to a SAM4S pin (say for battery monitoring) since this will cause an ESD protection diode inside the SAM4S to conduct.
5. Sometimes the program works but other times it does not The likely causes are:
(a) You have an uninitialised variable—check your code.
(b) You have a poor solder connection for a MCU pin—check with microscope.
(c) You have a race condition—this is unlikely unless you are using interrupts.

62 | CHAPTER 11. TROUBLESHOOTING

# Chapter 12

# Rework

Flux is your friend when doing rework. However, you need to remove it from your board when finished, see flux removal. You should check all rework with a magnifier and look for solder bridges.

## 12.1 Removing resistors and capacitors

1. Apply flux from syringe to pads.
2. Use tweezer soldering iron.

## 12.2 Removing larger parts

1. Apply flux from syringe to pads.
2. Use a grunty soldering iron. Do not push hard with a small soldering iron since this will bend the tips.

## 12.3 Removing MCU

1. Only remove as last resort.
2. Apply flux from syringe to all pins.
3. Get Scott to show you how to use the hot-air gun. The key is to choose a head that matches the size of the MCU and getting the temperature correct.
4. Be careful not to lift pads or tracks.

## 12.4 Adding a wire

1. For a signal trace, choose the very fine wire.
2. Cut to length and strip insulation from both ends. The second end is a lot harder!
3. Bend wire to shape and tape down to the PCB. Note, you can run this wire through vias.

63

64 | CHAPTER 12. REWORK
4. Apply flux from syringe to both pads.
5. Use small soldering iron to solder wires in place.

## 12.5 Flux removal

1. Scrub board with using flux-cleaner and brush.
2. Clean board with a towel.
3. Wash board with a little bit of IPA.
4. Clean board with a towel.

Show photos of clean board and dirty board

Show photos of rework grief

# Chapter 13

# Debugging

Your SAM4S can be debugged using OpenOCD in conjunction with GDB. However, debugging embedded systems is difficult due to asynchronous behaviour. Moreover, when optimising, a compiler will rearrange (and even remove) code and hold variables in registers.

## 13.1 Command-line debugging with GDB

If OpenOCD is running, a running program can be debugged using:

$ make debug

This starts GDB and attaches to the SAM4S. GDB is a command line debugger but there are many GUI programs that will control it, for example, vscode and geany have plugins.

GDB allows you to inspect the CPU registers, memory, set breakpoints, set watchpoints, and much more.

You can reset your program using the GDB jump reset command. However, this does not reset the peripherals as with a power-on reset.

The backtrace, bt, command is useful to show the function call stack.

65

66 | CHAPTER 13. DEBUGGING

# Appendix A

# OpenOCD

The Open On-Chip Debugger (OpenOCD) is an open-source on-chip debugging, in-system programming, and boundary-scan testing tool. It is able to communicate with various ARM and MIPS micro-processors via JTAG (http://ecewiki.elec.canterbury.ac.nz/mediawiki/index.php/JTAG) or SWD. (http://ecewiki.elec.canterbury.ac.nz/mediawiki/index.php/SWD) It works with a number of different JTAG (http://ecewiki.elec.canterbury.ac.nz/mediawiki/index.php/JTAG) or SWD (http://ecewiki.elec.canterbury.ac.nz/mediawiki/index.php/SWD) interfaces/programmers. User interaction can be achieved via telnet or the GNU debugger (GDB).

## A.1 Configuration files

OpenOCD needs a configuration file (http://ecewiki.elec.canterbury.ac.nz/mediawiki/index.php/OpenOCD_configuration) to specify the interface (USB or parallel port) and the target system. Unfortunately, these change with every new release of OpenOCD.

## A.2 Running OpenOCD

OpenOCD runs as a daemon program in the background and can be controlled from other programs using TCP/IP sockets. This means that you can remotely debug from another computer. The socket ports it uses are specified in the OpenOCD configuration (http://ecewiki.elec.canterbury.ac.nz/mediawiki/index.php/OpenOCD_configuration) file supplied when it starts. By default, OpenOCD uses port 3333 for GDB (http://ecewiki.elec.canterbury.ac.nz/mediawiki/index.php/GDB) and port 4444 for general interaction using Telnet.

A.2.1 Communicating with OpenOCD using telnet

If OpenOCD is running, commands can be sent to it using telnet. For example,

$ telnet localhost:4444
> monitor at91sam4s info

A.2.2 Communicating with OpenOCD using GDB

If OpenOCD is running, commands can be set to it with GDB. (http://ecewiki.elec.canterbury.ac.nz/mediawiki/index.php/GDB) There are two steps: connecting to OpenOCD with the target remote command, and then sending a command with the GDB monitor command. For example,

$ gdb
(gdb) target remote localhost:3333 (gdb) monitor flash info 0
| 67

68 | APPENDIX A. OPENOCD
A.3 | OpenOCD commands

All the gory OpenOCD details can be found in the OpenOCD manual. (http://ecewiki.elec.canterbury.ac.nz/mediawiki/index.php/Media:openocd.pdf) If you are getting strange errors see OpenOCD errors. (http://ecewiki.elec.canterbury.ac.nz/mediawiki/index.php/OpenOCD_errors)

## A.4 Flash programming

OpenOCD can program the flash program memory from a binary file.

## A.5 Errors

See OpenOCD errors. (http://ecewiki.elec.canterbury.ac.nz/mediawiki/index.php/OpenOCD_errors)

# Appendix B

# Git

To properly use git you should commit and push often. The smaller the changes and the more often you make per commit, the smaller the chance of the dreaded merge conflict.

## B.1 Typical workflow

1. Edit file
2. Save changes
3. Check differences

$ git diff .

4. Commit changes

$ git commit -m "Commit message" list-of-modified-files

Note, you should commit at least every 15 min, preferably when you have made a single functional change. Ideally each commit should be self-contained. Note, do not add binary files (.o) etc. These will make merging even more miserable.

5. Push changes to server

$ git push

The more often you push, the lower the chance that you will get a merge conflict.

## B.2 Diff, status, blame, log

The diff command is useful to determine what changes you made.

The status command says which files have been modified and what you should do, say when you get a merge conflict.

The blame command is useful to determine who authored each line of code.

The log command shows all the previous commit messages.

69

70 | APPENDIX B. GIT
B.3 | Pulling from upstream

To be able to get updates if the template project is modified you will need to:

$ cd wacky-racers
$ git remote add upstream https://eng-git.canterbury.ac.nz/wacky-racers/wacky-racers-2021.git

Again if you do not want to manually enter your password (and have ssh-keys uploaded) you can use:

$ cd wacky-racers
$ git remote add upstream
,→ git@eng-git.canterbury.ac.nz:wacky-racers/wacky-racers-2021.git

Once you have defined the upstream source, to get the updates from the main repository use:

$ git pull upstream master

If you enter the wrong URL by mistake, you can list the remote servers and delete the dodgy entry:

$ git remote -v
$ git remote rm upstream

Note, origin refers to your group project and upstream refers to the template project that origin was forked from.
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

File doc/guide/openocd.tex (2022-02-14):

\chapter{OpenOCD}
\label{OpenOCD}

The Open On-Chip Debugger (OpenOCD) is an open-source on-chip
debugging, in-system programming, and boundary-scan testing tool. It
is able to communicate with various ARM and MIPS microprocessors via
\wikiref{JTAG}{JTAG} or \wikiref{SWD}{SWD}. It works with a number of different
\wikiref{JTAG}{JTAG} or \wikiref{SWD}{SWD} interfaces/programmers. User
interaction can be achieved via telnet or the GNU debugger (GDB).

\section{Configuration files}
\label{configuration-files}
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

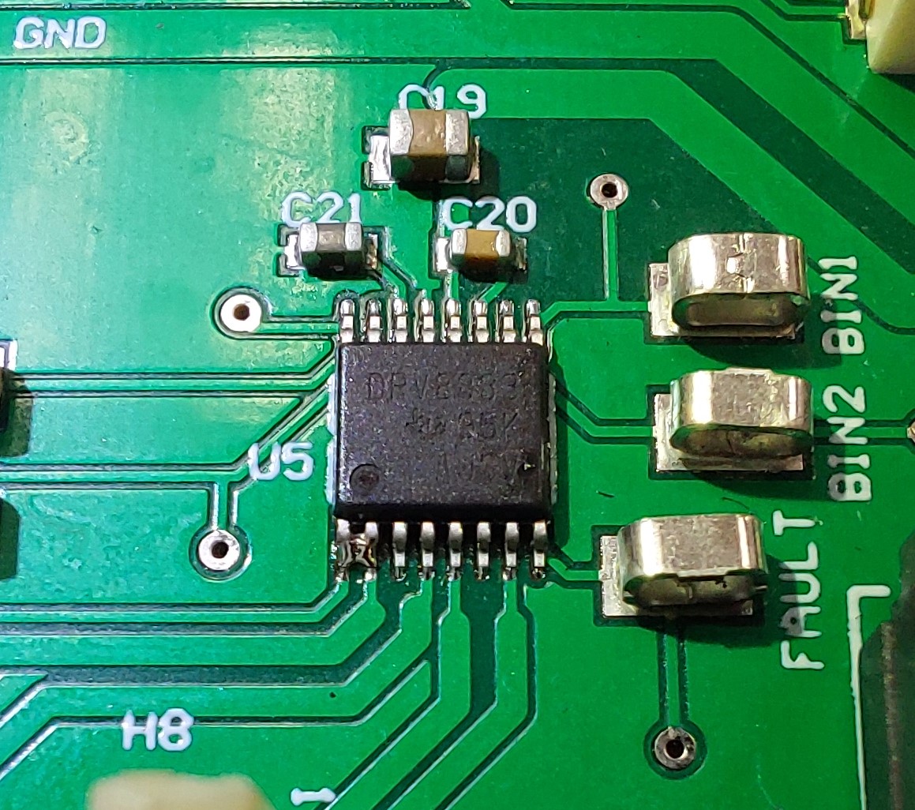
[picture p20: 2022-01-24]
doc/guide/figs/solder_bridge.jpg

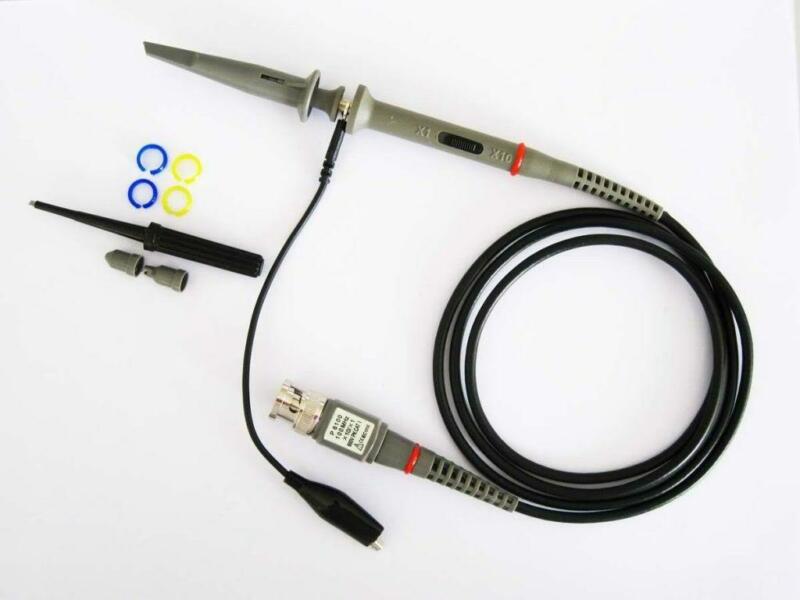
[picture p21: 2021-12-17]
doc/guide/figs/probe.jpg

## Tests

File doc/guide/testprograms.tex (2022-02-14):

\chapter{Test programs}
\label{test-programs}

There are a number of test programs in the directory
\wfile{test-apps}.  Where possible these are written to be
independent of the target board using configuration files (see
\protect\hyperref[configuration]{configuration}).

\section{USB}
\label{usb-interfacing}

To help debug your programs, it is useful to be able to print values.
This can be achieved by redirecting stdio using the \wikiref{USB
  CDC}{USB CDC} protocol.  For example, here's an example program
\wfile{test-apps/usb_serial_test1/usb_serial_test1.c}.

\inputminted{C}{../../src/test-apps/usb_serial_test1/usb_serial_test1.c}

To get this program to work you need to compile it and program the
SAM4S using:
%
\begin{minted}{bash}
$ cd wacky-racers/src/test-apps/usb_serial_test1
$ make program
\end{minted}

You then need to connect your computer to the USB connector on your PCB.
If you are running Linux, run:
%
\begin{minted}{bash}
$ dmesg
\end{minted}

This should say something like:
%
\begin{verbatim}
Apr 30 11:03:50 thing4 kernel: [52704.481352] usb 2-3.3: New USB device found, idVendor=03eb, idProduct=6202
Apr 30 11:03:50 thing4 kernel: [52704.481357] usb 2-3.3: New USB device strings: Mfr=1, Product=2, SerialNumber=3
Apr 30 11:03:50 thing4 kernel: [52704.482060] cdc_acm 2-3.3:1.0: ttyACM0: USB ACM device
\end{verbatim}

Congrats if you see \texttt{ttyACM0:\ USB\ ACM\ device}!  If not, see
\wikiref{USB_debugging}{USB debugging}.

You can now run a \wikiref{Serial_terminal_applications}{serial
  terminal program}. For example, on Linux:
%
\begin{minted}{bash}
$ gtkterm -p /dev/ttyACM0
\end{minted}

On the Windows machines in the ESL you can use Tera Term. On opening the
application, select the correct \code{COM} port from the \code{Serial}
dropdown. If there are multiple \code{COM} ports listed and you can't
tell which one belongs to the USB serial device, unplug the USB and
observe which \code{COM} port number is added to the dropdown menu when
you reinsert it.

All going well, this will repeatedly print `Hello world'.

If run Linux and get an error `device is busy', it is likely that the
ModemManager program has automatically connected to your device on the
sly. This program should be disabled on the ECE computers. For more
about this and using other operating systems, see \wikiref{USB
CDC}{USB CDC}.

\section{PWM}
\label{pwm-test}

The program \wfile{test-apps/pwm_test2/pwm_test2.c} provides an
example of driving PWM signals.

\inputminted{C}{../../src/test-apps/pwm_test2/pwm_test2.c}

Notes:
%
\begin{enumerate}
\item
  This is for a different H-bridge module that requires two PWM signals
  and forward/reverse signals. You will need to generate four PWM
  signals or be clever with two PWM signals.
\item
  The \code{pwm_cfg_t} structure configures the frequency, duty
  cycle and alignment of the output PWM.
\item The frequency is likely to be too high for your motor.
\item \code{pwm_channels_start} is used to start the PWM channels simultaneously.
\end{enumerate}

The most likely problem is that you have not used a PIO pin that can
be driven as a PWM output. The SAM4S can generate four independent
hardware PWM signals. See \wfile{mat91lib/pwm/pwm.c} for a list of
supported PIO pins. Note, \pin{PA16}, \pin{PA30}, and \pin{PB13} are
different options for PWM2.

To drive the motors you will need to use a bench power supply. Start
with the current limit set at 100\,mA maximum in case there are any
board shorts.  When all is well, you can increase the current limit;
you will need at least 1\,A.

\section{IMU}
\label{imu-test}

The MPU9250 IMU connects to the SAM4S using the I2C bus (aka TWI bus).
The program \wfile{test-apps/imu_test1/imu_test1.c} provides an
example of using the MPU9250 IMU.  All going well, this prints three
16-bit acceleration values per line to USB CDC. Tip your board over,
and the the third (z-axis) value should go negative since this
measures the effect of gravity on a little mass inside the IMU pulling
on a spring.

If you get `ERROR: can't find MPU9250!', the main reasons are:

\begin{enumerate}
\item
  You have specified the incorrect address.  Use 0x68 for
  \code{MPU_ADDRESS} in \file{target.h} if the AD0 pin is connected to
  ground otherwise use 0x69.
\item
  You are using TWI1. The \pin{PB4} and \pin{PB5} pins used by TWI1
  default to JTAG pins. See
  \protect\hyperref[disabling-jtag-pins]{disabling JTAG pins}.
\end{enumerate}
%
See also \protect\hyperref[checking-IMU]{IMU checking}.

Other problems:
%
\begin{enumerate}
\item If you reset the SAM4S in the middle of a transaction with the
IMU, the IMU gets confused and holds the \pin{TWD/SDA} line low. This
requires recycling of the power or sending out some dummy clocks on
the \pin{TWCK/SCL} signal.
\end{enumerate}

\section{Radio}
\label{radio-test}

The program \wfile{test-apps/radio_tx_test1/radio_tx_test1.c} provides
an example of using the radio as a transmitter.

The companion program
\wfile{test-apps/radio_rx_test1/radio_rx_test1.c} provides an example
of using the radio as a receiver.

\inputminted{C}{../../src/test-apps/radio_rx_test1/radio_rx_test1.c}

Notes:
%
\begin{enumerate}
\item Both programs must use the same RF channel and the same address.

\item Some RF channels are better than others since some overlap with
  WiFi and Bluetooth.

\item The address is used to distinguish devices operating on the same
  channel. Note, the transmitter expects an acknowledge from a
  receiver on the same address and channel.

\item The number of bytes that can be transmitted is set by the
  \code{payload\size} field in the configuration structure.  This has a
  maximum value of 32.

\item The radio `write` method blocks waiting for an
  auto-acknowledgement from the receiver device. This acknowledgement
  is performed in hardware. If no acknowledgement is received, it
  retries for up to 15 times. The auto-acknowledgement and number of
  retries can be configured in software.

\item If the program hangs in the \code{panic} loop, there is no
  response from the radio module, check SPI connections and see
  \hyperref[debugging-spi]{SPI debugging}.

\item The radio has two modes: transmit and receive.  Calling
  \code{nrf24_write} switches to transmit mode and calling
  \code{nrf24_read} switches to receive mode.

\end{enumerate}

If you cannot communicate between your hat and racer boards, try
communicating with the radio test modules Scott Lloyd has in the SMT
lab.

\section{ADC}
\label{ADC}

\wfile{test-apps/adc_usb_serial_test2/adc_usb_serial_test2.c} shows
how to read from two multiplexed ADC channels, specifically the hat joystick
channels (although it can be adapted for different purposes).  For more details
see \wfile{mat91lib/adc/adc.h}.

\inputminted{C}{../../src/test-apps/adc_usb_serial_test2/adc_usb_serial_test2.c}

The ADC can be also set up to stream data continuously but you need to
use interrrupts or DMA.

\section{Pushbutton}
\label{pushbutton}

\wfile{test-apps/button_test1/button_test1.c} shows the use of a
simple button driver to read a pushbutton.  This driver does not debounce the button.

\inputminted{C}{../../src/test-apps/button_test1/button_test1.c}

\wfile{test-apps/button_test2/button_test2.c} shows the use of a
simple button driver to read a pushbutton.  This driver does button
debouncing and state-transition detection.  For more details see
\wfile{mmculib/button/button.h}.

\inputminted{C}{../../src/test-apps/button_test2/button_test2.c}

\section{LEDtape}
\label{ledtape}

\wfile{test-apps/ledtape_test1/ledtape_test1.c} shows how to drive the
LEDtape.

\inputminted{C}{../../src/test-apps/ledtape_test1/ledtape_test1.c}

\wfile{test-apps/ledtape_test2/ledtape_test2.c} uses a more
sophisticated means of controlling the LEDs.

\inputminted{C}{../../src/test-apps/ledtape_test2/ledtape_test2.c}

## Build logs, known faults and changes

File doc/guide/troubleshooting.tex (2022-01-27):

\chapter{Troubleshooting}
\label{troubleshooting}

Troubleshooting can be frustrating when you are tired. You need plenty
of gumption and an open mind. Difficult problems are usually a
combination of two or more problems. So \textbf{do not attempt if you
  are tired or in a hurry}.

Before you start, you need an A3 printed schmematic, annotated with
any changes your group may have made.

\section{The scientific method}

Successful troubleshooting requires application of the scientific
method.  First you form a hypothesis about the cause of the problem
and then you test your hypothesis by making observations.  If the
observations do not confirm your hypothesis, you need to revise your
hypothesis and make more observations.

For example, let's say the IMU does not work.  A hypothesis is that
the chip has no power, so you test this by measuring the power supply
voltage at the chip with an \textbf{oscilloscope}.  But why not use a
multimeter?  Well, a multimeter only gives the average value and will
not show you that a voltage regulator is oscillating or if there is a
lot of noise.  If the power supply looks fine, you need another
hypothesis, say that the MCU is not outputting I2C signals.  You then
make observations of the I2C signals, with an oscilloscope, to see if
they are changing.  If the waveforms seem fine, you might hypothesise
that the IMU is not configured for the correct I2C address.  So you
then check that the acknowledge bit is driven low by the IMU.  If
there is no acknowledgement, you then check the address that the IMU
is configured for and the address sent over the I2C bus.  If these
match, you might hypothesise that there is a poor electrical
connection.  So you look at the soldering under a microscope, and so
forth.

When forming hypotheses, you need to start with the more likely ones.
Hypothesising that a chip is blown is unlikely unless you observed the
release of magic smoke, noticed that the chip got very hot, noticed an
electrostatic spark, or applied a high voltage, say by putting your
PCB on something conductive.

As you get more desperate, you need more outlandish hypotheses about
what may have gone wrong.  Here, experience helps.  However, the key
is forming a hypothesis based on previous observations\footnote{``Once
  you eliminate the impossible, whatever remains, no matter how
  improbable, must be the truth.'' --- Sherlock Homes.}.

\section{Reporting software errors}
\label{reporting-software-errors}

A common source of issues is improperly configured software; it is
helpful to catch these errors before getting out the oscilloscope and
probing the hardware. It is good coding practice to check the return
values of library functions for errors. For mmculib and mat91lib
library functions, read the function's implementation to determine
what value they return on failure. For standard library functions such
as \code{printf}, for example, read the man pages by running \code{man
3 printf} in the shell or Googling `man printf(3)'. Generally:
\begin{itemize}
\item Functions that return a pointer will return a \code{NULL}
pointer on failure.
\item Functions that return an integer will return 0 on success and a
negative integer on failure.
\end{itemize}

You should add a dedicated error LED to your board that you can flash
in an error state. For example, you could have a panic routine that
flashes the error LED every 400\,ms in an infinite loop:
\begin{minted}{C}
static void panic (void)
{
    pio_config_set (LED_ERROR_PIO, PIO_OUTPUT_LOW);
    while(1)
    {
        pio_output_toggle (LED_ERROR_PIO);
        delay_ms (400);
    }
}
\end{minted}
Then, say you are initialising a PWM module, you should check to see
if \code{pwm_init} returns a \code{NULL} pointer:
\begin{minted}{C}
pwm_t pwm1 = pwm_init (&pwm1_cfg);
if (! pwm1)
    panic ();
\end{minted}
You can also use the USB serial interface to report errors. However,
try to keep your panic routine simple to minimise the risk of an error
occurring during its execution!

It is even better if you can spot software bugs before programming
your board. Make sure you compile with the \code{-Wall} flag and
resolve any compiler warnings before programming.

\section{Oscilloscope}
\label{oscilloscope}

The best tool for debugging an embedded system is an oscilloscope.

\begin{enumerate}
\item  Use $\times$10 probes to reduce loading on the circuit.

\item Use the correct probes for the scope so that they can be automatically
  detected.

\item Compensate the probes by clipping to the probe test signal on
  the scope and adjusting the variable capacitor in the probe to
  ensure a square wave without undershoot or overshoot. This is one of
  the few times you are allowed to use the autoscale button!

\item Check that the probe gains are correct; they should by $\times
  10$ for $\times 10$ probes.

\item Hypothesise what you should expect to observe and set up the
  oscilloscope accordingly.  Pushing the auto-set button only works
  for AC or DC signals and is hopeless for transient signals, such as
  I2C bus waveforms.  For transient signals, use normal mode triggering.

\end{enumerate}

\begin{figure}[!h]
  \centering
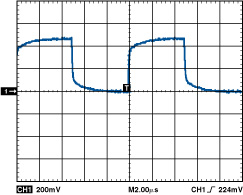
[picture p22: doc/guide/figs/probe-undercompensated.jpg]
  
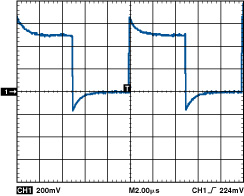
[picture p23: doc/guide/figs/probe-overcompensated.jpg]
  
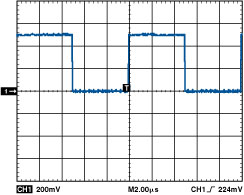
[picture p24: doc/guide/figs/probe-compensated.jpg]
  
  \caption{Oscilloscope probe compensation: under, over, and proper.
    From
    \url{http://www.analog.com/library/analogdialogue/archives/41-03/time_domain.html}.}
\end{figure}

\subsection{Normal mode}
\label{normal-mode}

This mode is for measuring transient or non-repetitive signals, such a
serial bus waveforms. It will only refresh the display if a trigger
event is detected.  You need to adjust the trigger level.

It is useful to increase the \emph{trigger holdoff} to prevent
triggering on multiple edges of a waveform.  By default, it is set to
a ridiculously small value.

\subsection{Auto mode}
\label{auto-mode}

This mode is for measuring AC or DC signals. It is like normal mode
but if it does not detect a trigger it will automatically refresh the
display.

\section{SAM4S not detected by OpenOCD}
\label{sam4s-not-detected-by-openocd}

If a program has not been loaded:

\begin{enumerate}
\item
  Check orientation of the SAM4S (the large circle does \textbf{not}
  mark pin 1).
\item
  Check soldering of the SAM4S pins under a microscope. Giving
  each pin a push with a sharp spike can reveal a poorly soldered joint.
\item
  Check 3.3\,V and 1.2\,V power rails.
\item
  Check the serial wire debug (SWD) signals, see
  \protect\hyperref[debugging]{debugging serial wire debug (SWD)}.
\end{enumerate}

If a program has been loaded:

\begin{enumerate}
\item  \protect\hyperref[checking-the-crystal-oscillator]{Check the
    crystal oscillator}.

\item \hyperref[erasing-flash-memory]{Erase flash memory}.

\item Re-enable \hyperref[booting-from-flash-memory]{booting from flash
  memory}.

\item  Reprogram the SAM4S with an LED flash program.
\end{enumerate}

\subsection{Erasing flash memory}
\label{erasing-flash-memory}

\begin{enumerate}
\item Connect the ERASE pin to 3.3\,V.

\item Re-start OpenOCD.

\item Re-enable \hyperref[booting-from-flash-memory]{booting from
  flash memory}.
\end{enumerate}

\subsection{Debugging serial wire debug (SWD)}
\label{debugging-serial-wire-debug-swd}

\program{OpenOCD} periodically polls to see if the SAM4S is alive.
These occur every 100\,ms, see \reffig{openocd-poll}.  If the SAM4S
responds, the waveform seen in \reffig{openocd-response} should be
observed on the SWD pin.

\begin{figure}[!h]
\centering

\caption{OpenOCD polls every 100\,ms while connected.}
\label{fig:openocd-poll}
\end{figure}

\begin{figure}[!h]
\centering

\caption{SWD signal when there is a response from the SAM4S.}
\label{fig:openocd-response}
\end{figure}

OpenOCD polls less often when it does not get a response. The period
increases to 6.3\,s.

\subsection{Checking the crystal oscillator}
\label{checking-the-crystal-oscillator}

When the SAM4S is first powered up it uses an internal RC oscillator.
However, when a program is loaded, the code before main is called
switches the SAM4S to use the main oscillator that uses the external
crystal.  If there is a problem with the crystal oscillator the SAM4S
will not run since it has no clock.  Moreover, \program{OpenOCD} will
then fail to communicate with the SAM4S.

\begin{figure}[!h]
\centering

\caption{12\,MHz clock sine wave measured on the XOUT pin.}
\label{fig:xout}
\end{figure}

\begin{figure}[!h]
  \centering
  \mtodo{Add scope picture of CPU clock signals when not working}
  \caption{Oscillator waveform when not working.}
\end{figure}

\begin{enumerate}
\item Connect a scope pin to the XOUT pin. A 12\,MHz sinewave should
  be visible, see \reffig{xout}.

\item If there is no sinewave:

  \begin{enumerate}
  \item Measure the voltage on the VDDPLL pin of the MCU with a
    scope. This should be 3.3\,V to power the oscillator.

  \item Check the bypass capacitors across the crystal.  These should
    be approx. 20 pF.
  \end{enumerate}
\end{enumerate}

\subsection{Checking the clock}
\label{checking-the-clock}

The SAM4s has multiple clock sources:

\begin{enumerate}
\item
  Internal fast RC oscillator (this is selected when the SAM4S is first
  ever used).
\item
  Internal slow RC oscillator (this can be selected to save power).
\item
  Main oscillator using external crystal.
\end{enumerate}

The SAM4S uses a phase-locked-loop (PLL) to multiply the frequency of
the clock source to provide the CPU clock. Sometimes the PLL will run
without a clock source and thus will generate an unexpected frequency.

The clock frequency can be checked by connecting a scope to a
peripheral pin that generates a clock, e.g., PWM, SCK, TXD, and
programming the peripheral.

\section{USB serial}
\label{debugging-usb}

USB is a complicated protocol and there are many possibilities why it
does not work.

  \begin{itemize}
  \item
    Check that the termination resistors are 27\,ohms.

  \item Check the SAM4S is running at the correct frequency of
    96\,MHz\footnote{The SAM4S has two PLLs so it is possible to clock
      the CPU at other frequencies.}.  Check the SAM4S XIN pin with an
    oscilloscope for a 12\,MHz sinusoid.  Note, the oscillator is not
    enabled unless a program has been loaded and running. If a 12\,MHz
    signal is not found, check the MCU solder connections under a
    microscope. Also check that the VDDPLL pin has 3.3\,V.
  \end{itemize}

  If the USB serial connection drops characters:
  %
 \begin{itemize}
 \item Add a delay before sending data.  This is because the driver
   takes a while to set up the connection after the USB cable is
   plugged in.  If you try to send some data during this time, the
   data gets stored into a ring buffer for later transmission.
   However, the ring buffer is not large and once it is filled, the
   USB serial driver will drop characters.
 \end{itemize}

\section{Motors}
\label{motors-testing}

For the motors to work:
%
\begin{enumerate}
\item The H-bridge must be correctly configured.
\item The PWM signals must be correctly generated.
\end{enumerate}

\subsection{Testing the H-bridge}
\label{testing-the-h-bridge}

\begin{enumerate}
\item The \sig{nFAULT} pin should be high.  Note, this is an
  open-drain pin and requires a pullup resistor to 3V3 to make it
  work.  Without this resistor, this pin will always read low, fault
  or no fault.  If this is connected to the SAM4S, it will be pulled
  up by default.

\item The \sig{nSLEEP} pin needs to be high to enable the chip.

\item Check that the capacitor connected to the \sig{INT} pin is
  2.2\,$\mu$F and not 2.2\,nF.

\item Check the \sig{AIN1}, \sig{AIN2}, \sig{BIN1}, \sig{BIN2} pins.
  If you see DC 2\,V, this is due to the signal not being configured
  as an output on the SAM4S; the internal pullup of the SAM4S forms a
  voltage divider with the internal pulldown of the H-bridge chip.

\item Check that \sig{AINSENSE} and \sig{BINSENSE} are connected
  directly to ground or to ground via a small resistor if you want
  current limiting.
\end{enumerate}

\subsection{Debugging PWM}
\label{debugging-pwm}

If PWM does not work:

\begin{enumerate}
\item
  Check the SAM4S pin since not every pin can be a PWM signal.
\item
  Check the definition in the configuration file \file{target.h}
\end{enumerate}

If the PWM frequency is wrong:

\begin{enumerate}
\item
  Check the clock frequency, see
  \hyperref[checking-the-clock]{checking the clock}.
\item
  Check your program.
\end{enumerate}

If the PWM duty is wrong:

\begin{enumerate}
\item
  Check your program. There are two ways to set the duty cycle with
  mat91lib's PWM module: (1) setting the \code{duty} field of the
  \code{pwm_cfg_t} struct using the \code{PWM_DUTY_DIVISOR} macro and
  passing the duty cycle as a percentage or (2) setting the
  \code{duty_ppt} field of the \code{pwm_cfg_t} struct as an integer
  in parts per thousand (e.g., 1000 = 100\% duty cycle; 50 = 5\% duty
  cycle). Setting the latter field will override the former. See the
  definition of \code{pwm_cfg_t} in \wfile{mat91lib/pwm/pwm.h}.
\end{enumerate}

\begin{figure}[!h]
\centering

\caption{Two PWM signals at 1\,kHz and 10\,kHz.}
\end{figure}

\section{IMU}
\label{imu}

For the IMU to work:
%
\begin{enumerate}
\item The IMU chip must be correctly configured.
\item The I2C bus must be working.
\end{enumerate}

\subsection{IMU checking}
\label{checking-IMU}

\begin{enumerate}
\item Check the I2C bus (see \hyperref[debugging-i2c]{debugging I2C}).
\item Check the auxiliary I2C bus signals are not connected on the IMU
  (otherwise the magnetometer will not respond).
\item Check \sig{nCS} on the IMU is pulled high.
\item Check \sig{FSYNC} on the IMU is pulled low.
\item Try pressing on a side of the IMU with a fingernail to see if it
  starts working; you might have a dry joint.  Otherwise look under
  the microscope at the pins of the IMU and touch them up with a
  soldering iron if necessary.
\item Check that you are using the correct I2C address corresponding
the the state of the AD0 pin (see datasheet).
\end{enumerate}

\subsection{Debugging I2C}
\label{debugging-i2c}

\begin{enumerate}
\item
  I2C/TWI requires external pull-up resistors for the clock (TCK) and
  data (TDA) signals.  Use a scope to look at the signals
  \pin{TWCK/SCL} and \pin{TWD/SDA}.  If the rise times are too slow so
  that the high voltage level is not 3.3\,V, the resistors are too
  large.
\item
  TWI channel 1 (TWI1) uses \pin{PB4} and \pin{PB5}. However, these
  are configured on boot as JTAG pins. You can disable this, see
  \hyperref[disabling-jtag-pins]{disabling JTAG pins}.
\end{enumerate}

\begin{figure}[!h]
  \centering
  \mtodo{Add scope picture of I2C signals}
  \caption{I2c signals with acknowledgement.}
\end{figure}

\begin{figure}[!h]
  \centering
  \mtodo{Add scope picture of I2C signals with no acknowledge}
  \caption{I2c signals with no acknowledgement.}
\end{figure}

\section{NRF24L01+ radio}
\label{nrf24l01-radio}

For the radio to work you need:

\begin{enumerate}
\item No ground planes near the antenna\footnote{You might have to
  mount the radio vertically.}.

\item A working SPI interface.

\item The correct channel and address.

\item A well filtered power supply for the radio, see \reffig{radio-filtering}.

\item A channel with little interference (note, some channels are
  shared with WiFi and Bluetooth and may be less reliable).
\end{enumerate}

If nothing works, check:

\begin{enumerate}
\item
  For transmission the CE pin should be low; for reception the CE pin
  should be high.
\item
  Check that the SPI clock SCK, MOSI, and MISO signals are driven when
  the radio is configured (note, the MISO signal is tristate when CS is
  high).
\item
  Check that the SPI CS signal is driven low for each transmitted byte.
\end{enumerate}

If the radio transmits but not receives, check:

\begin{enumerate}
\item
  The IRQ pin is driven low (this indicates that a packet has been
  received).
\item
  The power supply. The radio requires a well filtered power supply
  otherwise the range will be limited on reception. Preferably, the
  device should have its own 3V3 regulator with a low-pass RC filter
  comprised of a series resistor and large capacitor (say 22\,$\mu$F)
  or a low-pass LC filter made with a ferrite bead and capacitor.
\end{enumerate}

\textbf{Note}, by default the radio waits for an auto-acknowledgement
from the receiver device. This acknowledgement is performed in hardware.
If no acknowledgement is received, it retries for up to 15 times. The
auto-acknowledgement and number of retries can be configured in
software.

\subsection{Checking the radio power supply}
\label{checking-the-radio-power-supply}

\begin{figure}[!h]
  \centering
  \mtodo{Add scope picture of expected radio power supply voltage}
  \caption{Waveform showing radio power supply voltage.}
\end{figure}

\subsection{Debugging SPI}
\label{debugging-spi}

Check:
%
\begin{enumerate}
\item The device chip select signal is driven low.
\item The \pin{SCK} signal toggles while the chip select is low.
\item The \pin{MOSI} signal does something while the chip select is low.
\end{enumerate}
%
The \pin{MISO} signal is usually tri-state and is driven by the
device when the chip select is low.

The SPI standard is rather loose and there are four modes to confuse
the unwary; these are due to two clock polarity modes and two clock
phase modes.  When using the wrong mode, the read data can be out by a
bit or unreliable.

\begin{figure}[!h]
  \centering
  \mtodo{Add scope picture of SPI signals}
  \caption{SPI signals.}
\end{figure}

\section{Other problems}
\label{faq}

\begin{enumerate}
\item
  \emph{\program{OpenOCD} does not run}. The most common problem is
  that the USB permissions are not correct\footnote{On Linux this is
    controlled by udev.}.

\item
  \emph{A program does not correctly build after a file has been
    changed}. Every now and then the file timestamps are incorrect
  (this is a common problem with network drives due to a skew in the
  clocks) and make will not correctly rebuild a file. Running
  \textbf{make clean} will remove the existing dependency and object
  files so you can start afresh.

\item
  \emph{A program hangs.} This can be observed by an LED no longer
  flashing. There are a number of reasons:

  \begin{enumerate}
  \item
    The program is stuck in an infinite loop. Note, an embedded system
    should only have an infinite loop for the main loop; all other loops
    should have a timeout condition.
  \item
    The program has crashed trying to access invalid memory. Usually
    this is due to buffer overflow or dereferencing uninitialised
    pointers (say by not calling \code{radio_init}). Try running
    \code{make debug}.  This will start the
    \protect\hyperref[debugging]{debugger} and attach to your MCU. If
    the debugger says that your program has stopped in
    \code{_hardfault_handler}, then your program is likely to have
    accessed invalid memory. Use the \code{bt} command to print a
    stack trace to see how your program went astray.

  \item You are printing output using USB but a terminal program is
    not running.
  \end{enumerate}

\item
  \emph{The output of the 3V3 regulator works fine when powered from
    USB but gives 6\,V when powered from a 7.2\,V battery}. Check that
  the 7.2\,V is not connected directly to a SAM4S pin (say for battery
  monitoring) since this will cause an ESD protection diode inside the
  SAM4S to conduct.

\item \emph{Sometimes the program works but other times it does not}
  The likely causes are:
  %
  \begin{enumerate}
  \item You have an uninitialised variable---check your code.

  \item You have a poor solder connection for a MCU pin---check with
    microscope.

  \item You have a race condition---this is unlikely unless you are
    using interrupts.
  \end{enumerate}

\end{enumerate}

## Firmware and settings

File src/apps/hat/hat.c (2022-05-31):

/** @file   hat.c
    @author A. Musalov, A. Eason
    @date   4/05/2022
    @brief  Main code for the hat module

    To DO:
    -Sleep (needs to wakeup again - Angus)
    -LED tape (anton)
    -Buzzer somehthing small on hit (anton)
    -buzzer play anthem unblocked (Plays interesting sounds - Anton)
    -disable LED tape when low power
*/

/******************************************************************************
* INCLUDES
******************************************************************************/
#include "target.h"
#include "pio.h"
#include "delay.h"
#include "pacer.h"
#include "usb_serial.h"
#include "mpu9250.h"
#include "panic.h"
#include "mcu.h"
#include "app_radio.h"
#include "app_imu.h"
#include "hat.h"
#include "app_adc.h"
#include "app_pwm.h"
#include "app_gpio.h"
#include "adc.h"
#include "nrf24.h"
#include "spi.h"
#include "string.h"
#include "mcu_sleep.h"
#include "pwm.h"
#include "ledtape.h"
#include "ledbuffer.h"
#include <stdio.h>
#include "math.h"
#include "irq.h"
#include <stdlib.h>

/******************************************************************************
* CONSTANTS
******************************************************************************/
#define PACER_RATE 50 //Hz
#define SOUND_OFF_MAX   25

/******************************************************************************
* Globals
******************************************************************************/
// yellow, cyan, green, magenta, pink, blue, orange, white, violet
int my_colours[TOTAL_COLOURS][3] = {{255, 128, 0}, {0, 200, 70}, {50, 255, 0}, {255, 0, 255}, {255, 0, 100}, {0, 0, 255}, {255, 30, 0}, {255, 255, 255}, {70, 0, 255}};


int main (void)
{
    //---------------------Variables---------------------
    nrf24_t *nrf;
    mpu_t *mpu;
    int16_t accel[NUM_ACCEL_VALUES]; // For storing imu data
    uint16_t adc_data[NUM_ADC_CHANNELS]; // For storing adc data
    bool use_joy = false;
    pwm_t pwm1;
    pwm_t pwm2;
    int linear;
    int angular;
    int16_t x;       //Controll (imu or joy) raw data x
    int16_t y;       //Controll (imu or joy) raw data y
    int radio_ticks = 0;
    int led_ticks = 0;
    bool blue = true;
    int count_led = 0;
    int sound_off_ticks = SOUND_OFF_MAX;
    int sound_on_ticks = 2;
    int buzzer_ticks = 0;
    bool playing = 1;
    bool button_press = 0;

    
    
    //---------------------Peripheral setup---------------------
    // Redirect stdio to USB serial
    usb_serial_stdio_init (); // TO DO: disable this for assesment so it saves power in sleep

    pio_configuration();
    mpu = initialise_imu();
    initialise_adc();
    nrf = initialise_radio();
    pwm1 = init_pwm();
    pwm2 = init_pwm2();
    ledbuffer_t* leds = ledbuffer_init (LEDTAPE_PIO, NUM_LEDS);
    //---------------------Read configuration inputs---------------------
    
    use_joy = !pio_input_get (IMU_JOY_SEL);

    // ---------------------Setting up sleep----------------------------
    const mcu_sleep_wakeup_cfg_t sleep_wake_cfg = {  
        .pio = SLEEP_BUT_PIO,
        .active_high = false
    };
    if(!mcu_sleep_wakeup_set(&sleep_wake_cfg)) panic (LED_ERROR_PIO, INITIALISATION_ERROR);
    

    const mcu_sleep_cfg_t sleep_cfg = {  
        .mode = MCU_SLEEP_MODE_BACKUP //MCU_SLEEP_MODE_WAIT
    };

    //Flash LED to show everything initialised
    flash_led(LED_STATUS_PIO, 2);
    pacer_init (PACER_RATE); 
    uint8_t count = 0;
    while (1)
    {
        char temp_buffer[RADIO_TX_PAYLOAD_SIZE + 1];
        char tx_buffer[RADIO_TX_PAYLOAD_SIZE + 1]; // +1 for null terminator
        char rx_buffer[RADIO_RX_PAYLOAD_SIZE + 1]; // +1 for null terminator
        uint8_t rx_bytes;
        /* Wait until next clock tick.  */
        pacer_wait ();
        radio_ticks++;
        led_ticks++;
        buzzer_ticks++;

        if (led_ticks >= PACER_RATE*1) // 1s on 1s off
        {
            pio_output_toggle(LED_STATUS_PIO);
            led_ticks = 0;
        }
        //LED tape task
        if (low_bat_flag)
        {
            empty_strip();
        } else
        {
            if (count_led++ == NUM_LEDS)
            {
                // wait for a revolution
                ledbuffer_clear(leds);
                int colour_index = rand() % (TOTAL_COLOURS - 0 + 1);
                int r = my_colours[colour_index][0];
                int g = my_colours[colour_index][1];
                int b = my_colours[colour_index][2];
                if (blue)
                {
                    ledbuffer_set(leds, 0, r, g, b);
                    ledbuffer_set(leds, NUM_LEDS / 2, r, g, b);
                }
                else
                {
                    ledbuffer_set(leds, 0, 255, 0, 0);
                    ledbuffer_set(leds, NUM_LEDS / 2, 255, 0, 0);
                }
                //blue = !blue;
                count_led = 0;
            }
            ledbuffer_write (leds);
            ledbuffer_advance (leds, 1);
        }
        
        // Play anthem if switch in
        if (!pio_input_get (GPIO_JUMPER))
        {
            play_anthem(pwm1);
        }
        
        
        // Read IMU
        task_read_imu(mpu, accel);
        // Read all ADC (joystick and battery)
        task_read_adc(adc, adc_data, sizeof(adc_data));
        //printf("%i\n",ticks);
        // Set the x-y control values based on if we are using joystick or imu
        if (use_joy)
        {
            x = adc_data[1];
            y = adc_data[2];
        }else
        {
            x = accel[0];
            y = accel[1];
        }


        //printf("ximu = %d, yimu = %d, xjoy = %d, yjoy = %d\n", accel[0], accel[1], adc_data[1], adc_data[2]);
        //printf ("Bat = %d, x = %d, y = %d\n", adc_data[0], adc_data[1], adc_data[2]);

        //Convert IMU or joystick reading to scale 1-201 for x and y
        task_convert_imu_or_joy(&x, &y, &linear,&angular, use_joy);

        if (!pio_input_get(BUTTON))
        {
            button_press = 1;
        }
        //("%d\n", button_press);
        sound_off_ticks = SOUND_OFF_MAX - linear*SOUND_OFF_MAX/LINEAR_TRANFER_MAX + 1;
        if (playing)
        {
            if (buzzer_ticks >= sound_on_ticks)
            {
                pwm_channels_stop(pwm_channel_mask(pwm1));
                playing = 0;
                buzzer_ticks = 0;
            }
        } else
        {
            if (buzzer_ticks >= sound_off_ticks)
            {
                pwm_frequency_set (pwm1, 392 + linear);        
                pwm_channels_start (pwm_channel_mask (pwm1));
                playing = 1;
                buzzer_ticks = 0;
            }
        }

        
        // Convert int values into bytes and place into tx_buffer
        tx_buffer[0] = angular & 0xFF; 
        tx_buffer[1] = linear & 0xFF;
        if (button_press == 1)
        {
            tx_buffer[2] = 1 & 0xFF;
            button_press = 0;
        } else
        {
            tx_buffer[2] = 0 & 0xFF;
        }
        //printf("angular %i linear %i 69 %i\n", tx_buffer[0], tx_buffer[1], tx_buffer[2]);
        if (! nrf24_write (nrf, tx_buffer, RADIO_TX_PAYLOAD_SIZE)) 
        {
            //pio_output_set (LED_ERROR_PIO, 1);
        } else 
        {
            //pio_output_set (LED_ERROR_PIO, 0);
        }

        radio_ticks = 0;
        //pio_output_toggle (LED_ERROR_PIO);
         
        rx_bytes = nrf24_read (nrf, rx_buffer, RADIO_RX_PAYLOAD_SIZE); // Maybe buffer needs to be 3 long same as tx...
        if ((rx_bytes != 0) && (rx_buffer[0] == 1))
        {
            int flash_times = 0;
            printf ("%i\n", rx_buffer[0]);
            pio_output_toggle (LED_STATUS_PIO);

            play_card(pwm1);
            spin_flags(pwm2);
            nrf24_read (nrf, rx_buffer, RADIO_RX_PAYLOAD_SIZE);
            nrf24_read (nrf, rx_buffer, RADIO_RX_PAYLOAD_SIZE);
            nrf24_read (nrf, rx_buffer, RADIO_RX_PAYLOAD_SIZE);
            nrf24_read (nrf, rx_buffer, RADIO_RX_PAYLOAD_SIZE);
            rx_buffer[0] = 0;
        }
        

        if(low_bat_flag)
        {
            //disable LED tape...
            static int led_error_ticks = PACER_RATE/LOW_BAT_LED_RATE/2; // /2 as on for half period, off for half
            led_error_ticks--;
            if (led_error_ticks == 0)
            {
                pio_output_toggle (LED_ERROR_PIO);
                led_error_ticks = PACER_RATE/LOW_BAT_LED_RATE/2; // /2 as on for half period, off for half
            }
        } else pio_output_set (LED_ERROR_PIO, 0);
        
        
       



        // Poll sleep button and if pressed then sleep...
        if (!pio_input_get (SLEEP_BUT_PIO)) //sleep button pressed
        {
            // Do stuff to show we recieved the button press
            empty_strip();
            
            //delay_ms(500); // debounce button, not needed if playing sound       
            play_shutdown(pwm1);
            spin_flags(pwm2);
            pio_output_set (LED_STATUS_PIO, 0);
            pio_output_set (LED_ERROR_PIO, 0);

            //Shutdown peripherals
            nrf24_power_down (nrf);
            spi_shutdown(spi);

            //imu shutdown?
            twi_shutdown (mpu_twi);

            //Reconfigure all PIO as output low
            pio_sleep_mode();   

            //ADC shutdown
            //adc_shutdown(adc);

            // PWM
            pwm_shutdown();

            // Clear, then enable the interrupt
            pio_irq_clear (SLEEP_BUT_PIO);
            pio_irq_enable(SLEEP_BUT_PIO);
            irq_enable(PIO_ID(SLEEP_BUT_PIO));

            //Sleep mcu
            mcu_select_slowclock();
            mcu_sleep(&sleep_cfg);
            //Flash LED to show we wokeup
        }
    }

        
}

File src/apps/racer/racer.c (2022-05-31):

/** @file   racer.c
    @author E. Twomey, M. Gardyne
    @date   11 May 2022
    @brief  Kernel
    @note   -
*/


/******************************************************************************
* INCLUDES
******************************************************************************/
#include "target.h"
#include "motors.h"
#include "pacer.h"
#include "radio.h"
#include "usb_racer.h"
#include "racer_pio.h"
#include "racer_adc.h"
#include "ledtape.h"
#include "ledbuffer.h"
#include "mcu_sleep.h"
#include "pio.h"
#include "irq.h"

/******************************************************************************
* GLOBAL VARIABLES
******************************************************************************/
#define PACER_RATE 50 //Hz



/******************************************************************************
* TODO
******************************************************************************/
/*
- Always specify size eg (uint8_t)
- Typedef enum for motor states (DONE)
- Cut out if no packet recieved after ... amount of time
- Data packets 3 bytes (1 linear, 1 turn, 1 darstedly)
- Potential radio authentication? could be difficult (something like parity)
- Bumper clear send packet
- Broadcast many packets when bumper hit to ensure hat recieves
- Three point throttle curve
- Sleep
- Bat adc
*/

/******************************************************************************
* KERNEL
******************************************************************************/

int main (void)
{
    //---------------------Variables---------------------
    //nrf24_t *nrf;
    adc_t adc;
    uint16_t adc_data[NUM_ADC_CHANNELS]; // For storing adc data


    //---------------------Initialise Modules ---------------------
    init_pwm (); // Initalise PWM outputs
    init_pio (); // Initalise PIO
    adc = initialise_adc ();
    //nrf = initialise_radio (); // Initalise Radio
    initialise_radio (); // Initalise Radio
    usb_serial_t *usb_serial_1 = init_usb ();  // Initialise USB serial connection


    ledbuffer_t* leds = ledbuffer_init (LEDTAPE_PIO, NUM_LEDS);




    // ---------------------Setting up sleep----------------------------
    
    const mcu_sleep_wakeup_cfg_t sleep_wake_cfg = {  
        .pio = SLEEP_BUTTON_PIO,
        .active_high = false
    };
    
    if(!mcu_sleep_wakeup_set(&sleep_wake_cfg)) panic (LED_ERROR_PIO, INITIALISATION_ERROR);
    

    const mcu_sleep_cfg_t sleep_cfg = {  
        .mode = MCU_SLEEP_MODE_BACKUP //MCU_SLEEP_MODE_WAIT
    };
    



    // Status LED on
    //pio_config_set (LED_STATUS_PIO, PIO_OUTPUT_HIGH);

    
    // Set Motor values to zero
    //set_motor_vel (0, 0); // Start with motor off

    pacer_init (PACER_RATE); 
    int32_t ticks = 0;
    int count_led = 0;
    bool blue = false;
    int8_t turn_direction = 0;

    while (1) {

        ticks++;
        /* Wait until next clock tick.  */
        pacer_wait ();

        /* Run motor.  */ 
        //usb_to_motor (usb_serial_1);
        
        // Radio debug
        //printf("%d\n", nrf24_cfg.channel);

        /*
        if (count_led++ == NUM_LEDS)
        {
            // wait for a revolution
            ledbuffer_clear(leds);
            if (blue)
            {
                ledbuffer_set(leds, 0, 0, 0, 255);
                ledbuffer_set(leds, NUM_LEDS / 2, 0, 0, 255);
            }
            else
            {
                ledbuffer_set(leds, 0, 255, 0, 0);
                ledbuffer_set(leds, NUM_LEDS / 2, 255, 0, 0);
            }
            blue = !blue;
            count_led = 0;
        }
        ledbuffer_write (leds);
        ledbuffer_advance (leds, 1);


        if (count_led++ == 4)
        {
            ledbuffer_clear(leds);
            if (blue)
            {
                for (int led_num = 0; led_num < 12; led_num++) {
                    ledbuffer_set(leds, 0, 0, 255, 0);
                }
            }
            else
            {
                ledbuffer_clear(leds);
            }
        }
        */

        pio_output_toggle (LED_STATUS_PIO);
        read_adc(adc, adc_data, sizeof(adc_data));

        if (low_bat_flag)
        { 
            pio_config_set (LED_ERROR_PIO, PIO_OUTPUT_HIGH);
            empty_strip();
            pio_config_set(MOTOR_ENABLE_PIO, PIO_OUTPUT_LOW);
        } else 
        {
            pio_config_set (LED_ERROR_PIO, PIO_OUTPUT_LOW);
            pio_config_set(MOTOR_ENABLE_PIO, PIO_OUTPUT_HIGH);
        }
        
        if (!pio_input_get (BUMPER_SWITCH_PIO)) 
        {
            radio_transmit();
            set_motor_vel (101, 101);

            int flash_times = 0;
            while(flash_times < 9)
                {
                    empty_strip();
                    delay_ms(500);
                    red_strip();
                    delay_ms(500);
                    flash_times++;
                }
            set_motor_vel (101, 1);
            delay_ms(1000); 
            set_motor_vel (101, 101);
            
        } else {
            turn_direction = radio_recieve();
        }

        //empty_strip();

        //green_strip();
        if (ticks % 10 == 0) {
            blue = !blue;
        }

        if (turn_direction == TURN_LEFT) {
            if (blue) {
                indicate_left();
            } else {
                empty_strip();
            }
        } else if (turn_direction == TURN_RIGHT) {
            if (blue) {
                indicate_right();
            } else {
                empty_strip();
            }
        } else if (turn_direction == FWD) {
            if (blue) {
                indicate_fwd();
            } else {
                empty_strip();
            }
        } else if (turn_direction == REV) {
            if (blue) {
                red_strip();
            } else {
                empty_strip();
            }
        } else {
            green_strip();
        }


        // Poll sleep button and if pressed then sleep...
        // if (!pio_input_get (SLEEP_BUTTON_PIO) && (ticks >= 100)) //sleep button pressed
        // {
        //     // Do stuff to show we recieved the button press
        //     red_strip();
        //     pio_output_set (LED_STATUS_PIO, 0);
        //     pio_output_set (LED_ERROR_PIO, 0);

        //     delay_ms(1000);

        //     // Try enable the interrupt
        //     pio_irq_clear(SLEEP_BUTTON_PIO);
        //     pio_irq_enable(SLEEP_BUTTON_PIO);
        //     irq_enable(PIO_ID(SLEEP_BUTTON_PIO));

        //     pio_sleep_mode();   
        //     empty_strip();

        //     //Sleep mcu
        //     mcu_select_slowclock();
        //     mcu_sleep(&sleep_cfg);


        //     //Flash LED to show we wokeup
        //     flash_led(LED_STATUS_PIO, 5);
        //     pio_config_set(SLEEP_BUTTON_PIO, PIO_OUTPUT_HIGH);
        //     ticks = 0;
        // }
	}
}

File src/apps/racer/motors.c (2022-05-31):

/** @file   motors.c
    @author E. Twomey, M. Gardyne
    @date   4 May 2022
    @brief  Motor PWM Control
    @note   Needs completing
*/

/* Take signed int from -10-10 for linear and same for angular
*/



/******************************************************************************
* INCLUDES
******************************************************************************/

#include "motors.h"
#include <math.h>



/******************************************************************************
* GLOBAL VARIABLES
******************************************************************************/

#define LINEAR_GAIN 1
#define REVERSE_GAIN 2
#define ANGULAR_GAIN 1
#define Y_GAIN_V2 0.0001
#define X_GAIN_V2 0.0001
#define ZONE 20
#define MAX_DUTY 100
#define MIN_DUTY -100

typedef enum
{
    LEFT,
    RIGHT
} motor;




/******************************************************************************
* PWM STRUCTURES
******************************************************************************/

static const pwm_cfg_t pwmL1_cfg =
{
    .pio = MOTOR_LEFT_FORWARD_PWM_PIO,
    .period = PWM_PERIOD_DIVISOR (PWM_FREQ_HZ),
    .duty = PWM_DUTY_DIVISOR (PWM_FREQ_HZ, 50),
    .align = PWM_ALIGN_LEFT,
    .polarity = PWM_POLARITY_HIGH,
    .stop_state = PIO_OUTPUT_LOW
};

static const pwm_cfg_t pwmL2_cfg =
{
    .pio = MOTOR_LEFT_BACKWARD_PWM_PIO,
    .period = PWM_PERIOD_DIVISOR (PWM_FREQ_HZ),
    .duty = PWM_DUTY_DIVISOR (PWM_FREQ_HZ, 50),
    .align = PWM_ALIGN_LEFT,
    .polarity = PWM_POLARITY_HIGH,
    .stop_state = PIO_OUTPUT_LOW
};

static const pwm_cfg_t pwmR1_cfg =
{
    .pio = MOTOR_RIGHT_FORWARD_PWM_PIO,
    .period = PWM_PERIOD_DIVISOR (PWM_FREQ_HZ),
    .duty = PWM_DUTY_DIVISOR (PWM_FREQ_HZ, 50),
    .align = PWM_ALIGN_LEFT,
    .polarity = PWM_POLARITY_HIGH,
    .stop_state = PIO_OUTPUT_LOW
};

static const pwm_cfg_t pwmR2_cfg =
{
    .pio = MOTOR_RIGHT_BACKWARD_PWM_PIO,
    .period = PWM_PERIOD_DIVISOR (PWM_FREQ_HZ),
    .duty = PWM_DUTY_DIVISOR (PWM_FREQ_HZ, 50),
    .align = PWM_ALIGN_LEFT,
    .polarity = PWM_POLARITY_HIGH,
    .stop_state = PIO_OUTPUT_LOW
};



/******************************************************************************
* INTIALISE PWM
******************************************************************************/

void init_pwm (void)
{
    // Initialise PWM channels left hand and right hand sides
    //pio_config_set (LED_STATUS_PIO, PIO_OUTPUT_HIGH);
    // H-Bridge enable 
    pio_config_set (MOTOR_ENABLE_PIO, PIO_OUTPUT_HIGH);

    pwmL1 = pwm_init (&pwmL1_cfg);
    if (! pwmL1)
        panic (LED_ERROR_PIO, 1);

    pwmL2 = pwm_init (&pwmL2_cfg);
    if (! pwmL2)
        panic (LED_ERROR_PIO, 2);

    pwmR1 = pwm_init (&pwmR1_cfg);
    if (! pwmR1)
        panic (LED_ERROR_PIO, 3);

    pwmR2 = pwm_init (&pwmR2_cfg);
    if (! pwmR2)
        panic (LED_ERROR_PIO, 4);
    
}


/******************************************************************************
* SET PWM (from duty cycle)
******************************************************************************/

void set_pwm(uint8_t motor, int32_t duty) {
    // Set PWM for desired motor based on velocity input
    switch (motor)
    {
    case LEFT:
        if (duty > 0) {
            pwm_duty_set (pwmL1, PWM_DUTY_DIVISOR (PWM_FREQ_HZ, duty));
            pwm_stop (pwmL2);
            pwm_start (pwmL1);   
        } else {
            //pio_config_set (LED_STATUS_PIO, PIO_OUTPUT_HIGH);
            //pwm_duty_set (pwmL2, PWM_DUTY_DIVISOR (PWM_FREQ_HZ, -vel));
            pwm_duty_set (pwmL2, PWM_DUTY_DIVISOR (PWM_FREQ_HZ, -duty));
            pwm_stop (pwmL1);
            pwm_start (pwmL2); 
        }
        break;
    
    case RIGHT:
        if (duty > 0) {
            pwm_duty_set (pwmR1, PWM_DUTY_DIVISOR (PWM_FREQ_HZ, duty));
            pwm_stop (pwmR2);
            pwm_start (pwmR1);   
        } else {
            pwm_duty_set (pwmR2, PWM_DUTY_DIVISOR (PWM_FREQ_HZ, -duty));
            pwm_stop (pwmR1);
            pwm_start (pwmR2);
        }
        break;
    }
}



/******************************************************************************
* SET MOTOR VELOCITY (from x & y velocity)
******************************************************************************/

void set_motor_vel (int16_t x_vel, int16_t y_vel) {
    // Set motor velocities based on recieved radio commands. 
    int32_t left_motor_duty = 0;
    int32_t right_motor_duty = 0;


    // VERSION ONE: No deadzone
    y_vel = y_vel - 101;
    x_vel = x_vel - 101;

    if ((x_vel < 50) || (x_vel > -50)) {
        x_vel = x_vel*ANGULAR_GAIN;
    }
    if (y_vel > 0) {
        left_motor_duty = REVERSE_GAIN*(y_vel) + (x_vel);
        right_motor_duty = REVERSE_GAIN*(y_vel) - (x_vel);
    } else {
        left_motor_duty = LINEAR_GAIN*(y_vel) - (x_vel);
        right_motor_duty = LINEAR_GAIN*(y_vel) + (x_vel);
    }
    

    // VERSION TWO: Approximate deadzone using non-linear gain. (WORKING)

    //left_motor_duty = Y_GAIN_V2*pow(y_vel,3) + X_GAIN_V2*pow(x_vel,3);
    //right_motor_duty = Y_GAIN_V2*pow(y_vel,3) - X_GAIN_V2*pow(x_vel,3);


    //left_motor_duty = set_deadzone (left_motor_duty);
    //right_motor_duty = set_deadzone (right_motor_duty);
    left_motor_duty = limit_val (left_motor_duty);
    right_motor_duty = limit_val (right_motor_duty);
    //printf("%d\n", left_motor_duty);
    //printf("%d\n", right_motor_duty);


    set_pwm(LEFT, left_motor_duty);
    set_pwm(RIGHT, right_motor_duty); 
}




/******************************************************************************
* SET DEADZONE AND MAXIMUMS TO DUTY CYCLE
******************************************************************************/

int32_t set_deadzone (int32_t duty_cycle) {

    // VERSION THREE: Hard coded deadzone (run with version 1).

    if (duty_cycle < -ZONE/2) {
        duty_cycle = duty_cycle + ZONE/2;
    } else if (duty_cycle > ZONE/2) {
        duty_cycle = duty_cycle - ZONE/2;
    } else {
        duty_cycle =0;
    }

    if (duty_cycle > 100) {
        duty_cycle = 100;
    } else if (duty_cycle < -100) {
        duty_cycle = -100;
    }

   return duty_cycle;
}

int32_t limit_val (int32_t duty_cycle) {

    // VERSION THREE: Hard coded deadzone (run with version 1).

    if (duty_cycle >= MAX_DUTY) {
        duty_cycle = MAX_DUTY;
    } else if (duty_cycle <= MIN_DUTY) {
        duty_cycle = MIN_DUTY;
    }

   return duty_cycle;
}


/******************************************************************************
* USB CONTROL OF MOTORS
******************************************************************************/
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

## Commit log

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2021-05-24 Add notes about ADC
2021-12-17 Add openocd fig
    [openocd.sch]
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2022-01-25 Fix LED names
2022-01-27 radio_tx_test1: fix potential buffer overrun
    [radio_tx_test1.c]
2022-01-27 boards: hat: change ADC macros to use ADC channels rather than PIO
2022-01-27 guide: testprograms: update ADC test program
2022-01-27 guide: troubleshooting: more info on software, PWM, and I2C debugging
2022-01-27 Add LED tape photo
2022-01-27 pwm_test2: set polarity of both outputs to high
2022-01-27 Remove SPI config from nrf24 driver
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2022-02-24 Racer Schematic
    [MCU.SchDoc, racer.PrjPcb]
2022-02-24 Adding Hat schematic and project
    [Hat.PrjPcb, MCU.SchDoc]
2022-02-25 Updated racer schematic
    [MCU.SchDoc]
2022-02-25 Added analogue 3v3 regulation, battery + LED connectors, buck converter (not external circuit yet)
    [MCU.SchDoc]
2022-02-25 Update racer schematic
    [MCU.SchDoc]
2022-03-01 Added DataSHeets
    [MCU.SchDoc]
2022-03-01 added IMU, level shifter, fuse and zener
    [MCU.SchDoc]
2022-03-01 Label change
    [MCU.SchDoc]
2022-03-02 Added 0R resistors and testpoints to Hat. Also added LPF to the radio connector
    [MCU.SchDoc]
2022-03-02 Push before changes
    [MCU.SchDoc]
2022-03-02 COmmiting for safetyy
    [MCU.SchDoc]
2022-03-02 Made Changes to Schematic - Added Joystick Connector and two extra 5V PWM signals for Darstadly stuff if needed. Only made changes to helmet schematic
    [MCU.SchDoc]
2022-03-02 Angus working on TO DO list, buzzer, jumpers etc
    [MCU.SchDoc]
2022-03-02 Racer update
    [MCU.SchDoc]
2022-03-02 Added 5V regulation circuitry
    [MCU.SchDoc]
2022-03-03 Racer Schematic semi done
    [MCU.SchDoc]
2022-03-03 First draft of schematic complete
    [MCU.SchDoc]
2022-03-03 Angus checkover Hat schematic
    [MCU.SchDoc]
2022-03-03 Tweaking small things on racer and hat
    [MCU.SchDoc]
2022-03-04 Mark Review
    [MCU.SchDoc]
2022-03-04 Small changes to hat schematic
    [MCU.SchDoc]
2022-03-08 Changed dir pin on level shifters to make inputs on left, outputs on right. moved testpoints onto signals
    [MCU.SchDoc]
2022-03-08 Changes from micheals tut
    [MCU.SchDoc]
2022-03-09 Adding PD res on RADIO_CE and importing pcb template
    [MCU.SchDoc, hat.PcbDoc]
2022-03-09 Annotations saved
    [MCU.SchDoc, hat.PcbDoc]
2022-03-09 Start of pcb layout done
    [Hat.PrjPcb, MCU.SchDoc, hat.PcbDoc]
2022-03-11 Adjusted tp
    [MCU.SchDoc]
2022-03-11 Fix ups
    [MCU.SchDoc]
2022-03-11 fixing testpoints briding
    [MCU.SchDoc]
2022-03-12 Modifications to Hat PCB
    [MCU.SchDoc, hat.PcbDoc]
2022-03-13 Minor schematic changes
    [hat.PcbDoc]
2022-03-14 Addec decoupling caps for level shifters, moved some componets around
    [MCU.SchDoc, hat.PcbDoc]
2022-03-14 Changes to racer PCB
    [MCU.SchDoc, racer.PrjPcb, racer_pcb.PcbDoc]
2022-03-14 Layout of PCB
    [Hat.PrjPcb, MCU.SchDoc, hat.PcbDoc]
2022-03-14 PCB layout changes
    [Hat.PrjPcb, MCU.SchDoc, hat.PcbDoc]
2022-03-15 Schematic changes
    [MCU.SchDoc, hat.PcbDoc]
2022-03-15 Fixed level shifters power and datas, moved components in frfom edge on schematic, added names to PCB
    [MCU.SchDoc, hat.PcbDoc]
2022-03-15 Racer PCB update
    [MCU.SchDoc, racer_pcb.PcbDoc]
2022-03-15 Final check and change before routing
    [MCU.SchDoc, hat.PcbDoc]
2022-03-16 Racer pcb change
    [MCU.SchDoc, racer_pcb.PcbDoc]
2022-03-16 PCB wiring
    [Hat.PrjPcb, hat.PcbDoc]
2022-03-16 PCB routing
    [MCU.SchDoc, hat.PcbDoc]
2022-03-16 moving things around on PCB
    [hat.PcbDoc]
2022-03-16 Started routing on the racer PCB
    [MCU.SchDoc, racer_pcb.PcbDoc]
2022-03-16 Decoupling caps, high freq, power all routed on hat
    [Hat.PrjPcb, MCU.SchDoc, hat.PcbDoc]
2022-03-17 Wiring HAt PCB
    [MCU.SchDoc, hat.PcbDoc]
2022-03-17 Moved 5V all together, buzzer top right
    [MCU.SchDoc, hat.PcbDoc]
2022-03-18 Added new wiring
    [MCU.SchDoc, hat.PcbDoc]
2022-03-18 Checked over some of PCB, should have most routing done other than ground
    [MCU.SchDoc, hat.PcbDoc]
2022-03-18 Check over schematic and pcb layout
    [MCU.SchDoc, hat.PcbDoc]
2022-03-18 Adding GND vias to decoupling caps
    [hat.PcbDoc]
2022-03-19 Fixing Errors
    [MCU.SchDoc, hat.PcbDoc]
2022-03-19 Racer PCB and Schematic mods
    [MCU.SchDoc, racer_pcb.PcbDoc]
2022-03-19 Finnishing routing racer PCB
    [MCU.SchDoc, racer_pcb.PcbDoc]
2022-03-20 All design rule checks gone, no ground top pour
    [hat.PcbDoc]
2022-03-20 Angus went over checklist, moved ground testpoints to better spots, made mounting holes on standard positions
    [hat.PcbDoc]
2022-03-20 Fixing up some DRC errors
    [MCU.SchDoc, racer_pcb.PcbDoc]
2022-03-20 Removing GND pour from around radio
    [hat.PcbDoc]
2022-03-20 Fixing merge that deleted everything
    [Hat.PrjPcb, MCU.SchDoc]
2022-03-20 Adding bulk decoupling on USB input
    [MCU.SchDoc, hat.PcbDoc]
2022-03-20 Last changes to PCB
    [MCU.SchDoc, racer_pcb.PcbDoc]
2022-03-20 Moved joystick and channel select traces to reduce loops
    [hat.PcbDoc]
2022-03-20 FInal Check added one mounting hole
    [hat.PcbDoc]
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2022-04-22 Proper bom'
    [Hat.xls]
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2022-04-24 Slight modifcations to some test files. IMU did not work and have not tested radio
    [MCU.SchDoc]
2022-05-03 Should have added micheals patch for the IMU, I did it manually tho so might be wrong. Still doesnt work as we cant even initialise the TWI bus
    [imu_test1.c, mpu9250.c]
2022-05-03 Fixed IMU problem
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2022-05-05 Added working motor.c and motor.h to racer, added TODO list, fixed led tape, added control method to interpret recieved values and gains
    [motors.c, racer.c]
2022-05-05 Added IMU decoder to convert raw to a range of 0-20. Radion now sends 3 bytes - byte 1 = 0-20 linear - byte 2 = 0-20 angular byte 3 = dastradly stuff. 10 is in resting position.
2022-05-08 Changing radio channel works, fixed uart not working
    [app_adc.c, app_radio.c, hat.c]
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2022-05-11 Pushing end of session, radio not working
    [hat.c, radio_tx_test1.c]
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2022-05-11 Added Card Buzzer Noise
    [pwm_test2.c]
2022-05-11 Added shutdown noise and LED tape into main
    [app_pwm.c, app_pwm.h, hat.c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]
2022-05-12 Battery level
    [MCU.SchDoc]
2022-05-12 Battery flash indicator (needs to be tested with battery) and joystick encoded to values
2022-05-13 Added deadzone, max motor PWM, backwards motor funct and changes some radio stuff
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2022-05-14 Fixed radio connection issue and added 0xFF back
    [hat.c]
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2022-05-18 Added flucuating LED Tape through loop - And red flash on bumper hit - untested
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2022-05-21 Tring new sleep stuff, level interrupt and actually having an interrupt handler
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2022-05-23 PIO radio pins made output low, might have broken it and probably doesnt save any power since radio is still powered
    [app_gpio.c]
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2022-05-26 Adding beep relative to forward speed, fixed green LED flash rate
    [hat.c]
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2022-05-31 Fixed LED
2022-05-31 flipped turning to drive reverse
    [app_imu.h, motors.c]
